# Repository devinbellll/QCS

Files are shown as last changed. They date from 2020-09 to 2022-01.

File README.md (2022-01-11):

# QCS (Quadcopter Control System)
A stabilization and flight control system for a quadcopter, developed in MATLAB and Simulink.

See embedded development and PCB design repo [here](https://github.com/adambujak/FALCON).

Done in collaboration with Adam Bujak ([@adambujak](https://github.com/adambujak) - McMaster University - Mechatronics Engineering).

# Highlights from Development

[Motor Testing and Characterization](https://github.com/devinbellll/QCS/tree/master/Testing/ThrottleSpeedTest)

[Rotor Testing and Characterization](https://github.com/devinbellll/QCS/tree/master/Testing/RotorTest)

## Characterizing the rotor power profile for system modeling

https://user-images.githubusercontent.com/47790946/148705799-1a313020-7e75-4045-ad6e-294311040c41.mp4

## Custom PCB arrived from California courtesy of Adam Bujak

PCB

## First desk-top test on 3D-printed test stand

https://user-images.githubusercontent.com/47790946/148705807-855fa435-2b67-44c3-ac4a-68730c8c19b8.mp4

## Flight Control System stabilizing drone on test stand without assistance

https://user-images.githubusercontent.com/47790946/148705802-f173073f-fe2c-465a-9571-49fa52ba8208.mp4

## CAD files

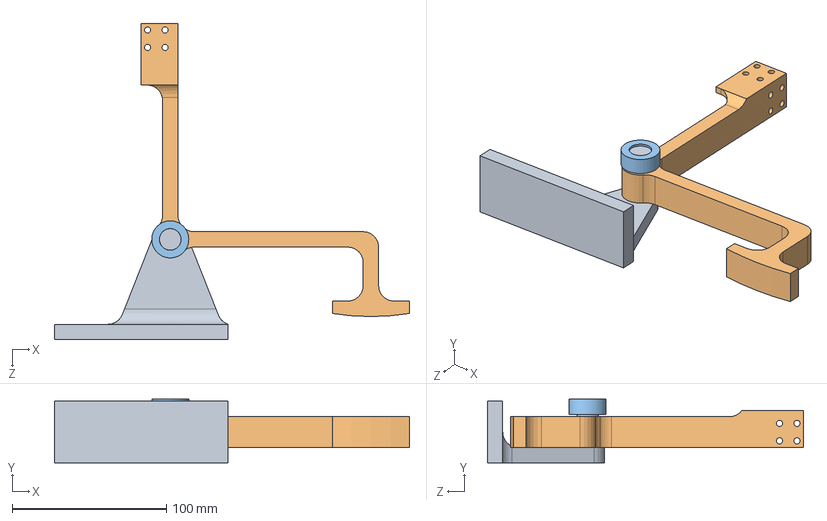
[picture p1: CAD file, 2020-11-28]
Testing/RotorTest/Models/RotorTestRig.SLDASM
230.0 x 41.4 x 205.0 mm
Base
Lever
Cap

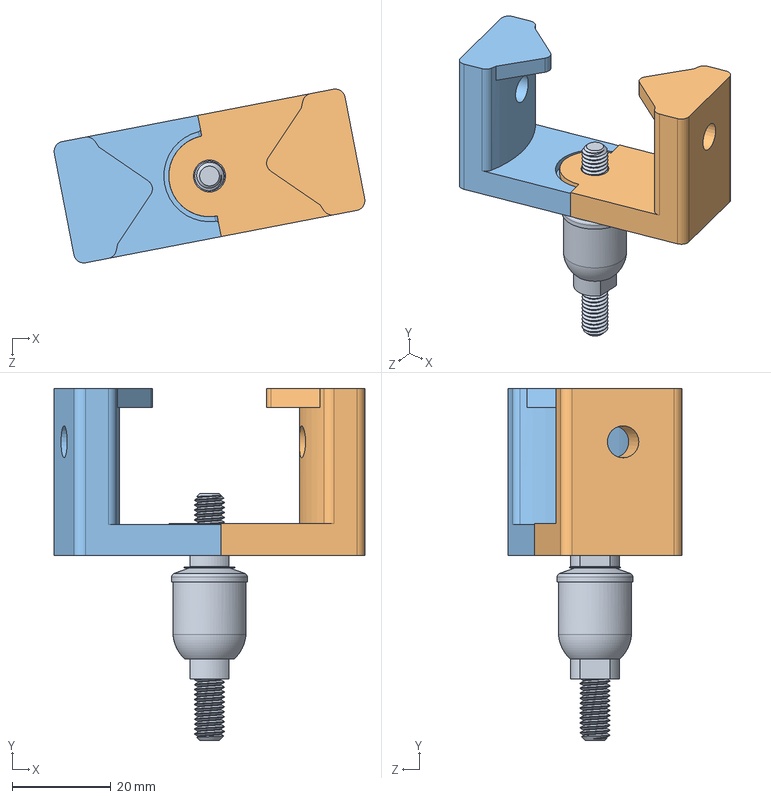
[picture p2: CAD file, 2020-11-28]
Testing/TestStand/TestStand.SLDASM
63.0 x 71.3 x 35.2 mm
BallJoint
DroneMountBracket_d
DroneMountBracket_s

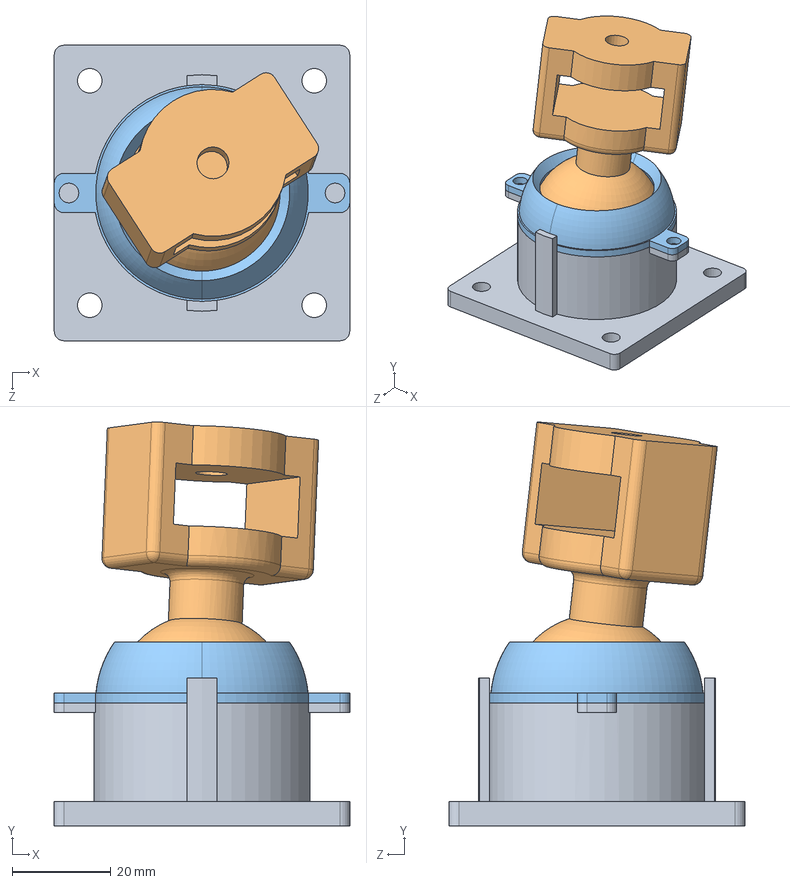
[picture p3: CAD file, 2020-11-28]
Testing/TestStand/TestBallJoint.SLDASM
60.0 x 82.0 x 60.0 mm
Socket
Ball
SocketCap x 2

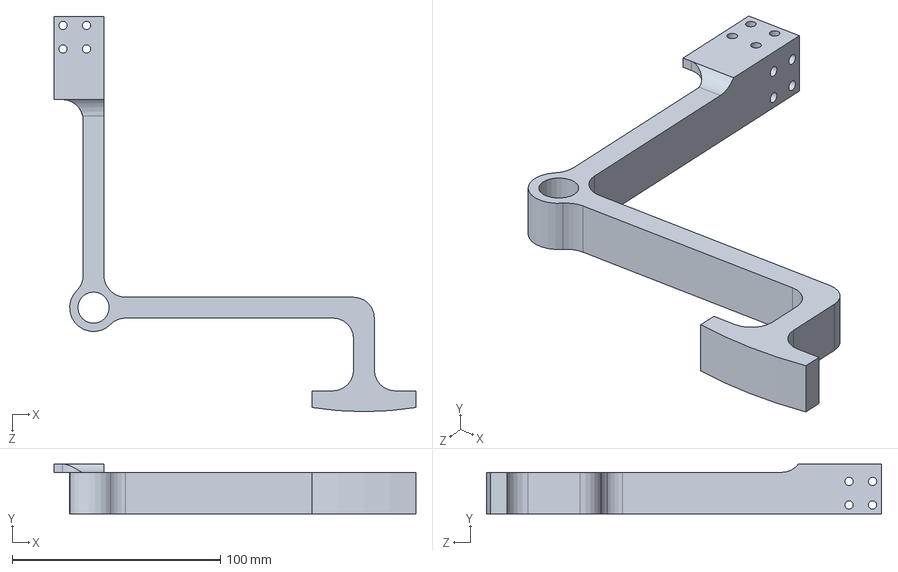
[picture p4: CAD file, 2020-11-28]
Testing/RotorTest/Models/Lever.SLDPRT
174.0 x 24.0 x 190.0 mm

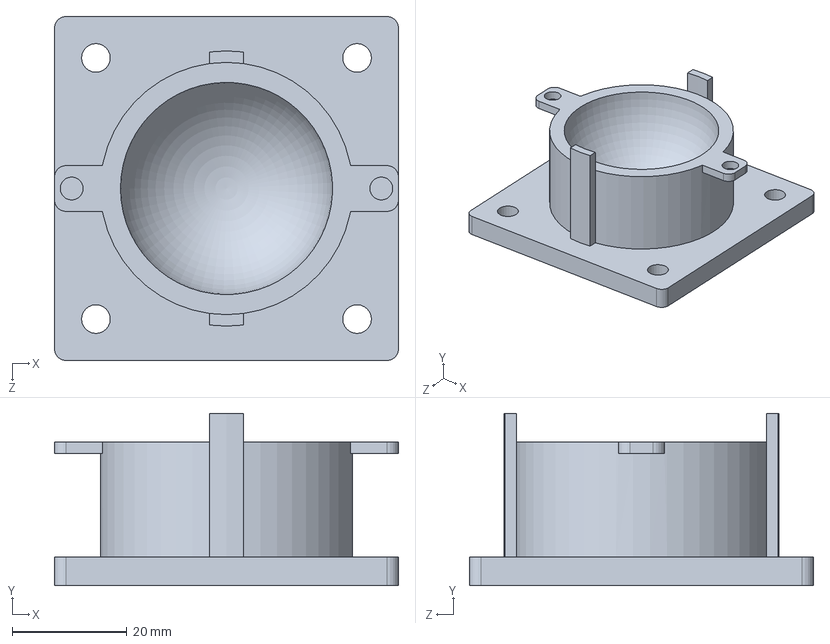
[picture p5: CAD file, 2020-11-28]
Testing/TestStand/Socket.SLDPRT
60.0 x 30.0 x 60.0 mm

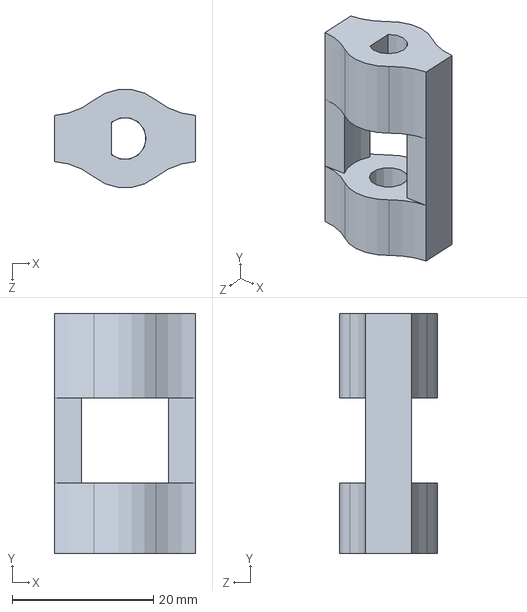
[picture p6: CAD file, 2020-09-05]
Testing/ThrottleSpeedTest/Models/speedTestCoupling.SLDPRT
20.0 x 34.0 x 13.9 mm

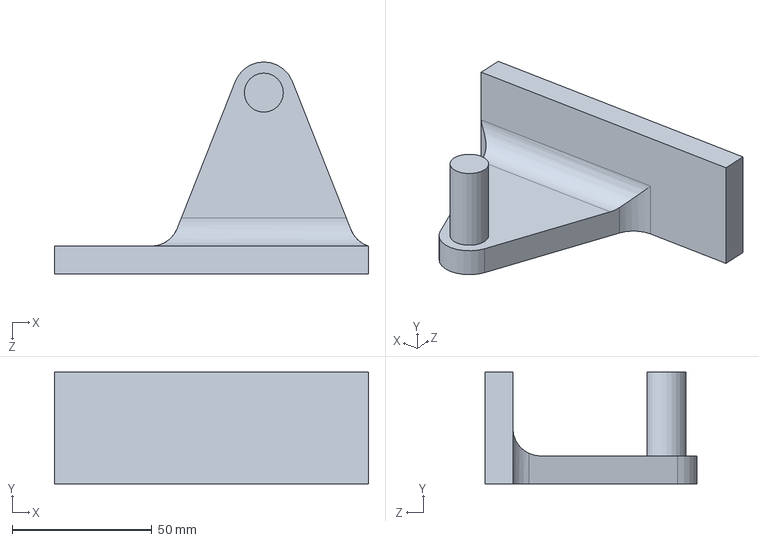
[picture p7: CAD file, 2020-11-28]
Testing/RotorTest/Models/Base.SLDPRT
112.5 x 40.0 x 76.0 mm

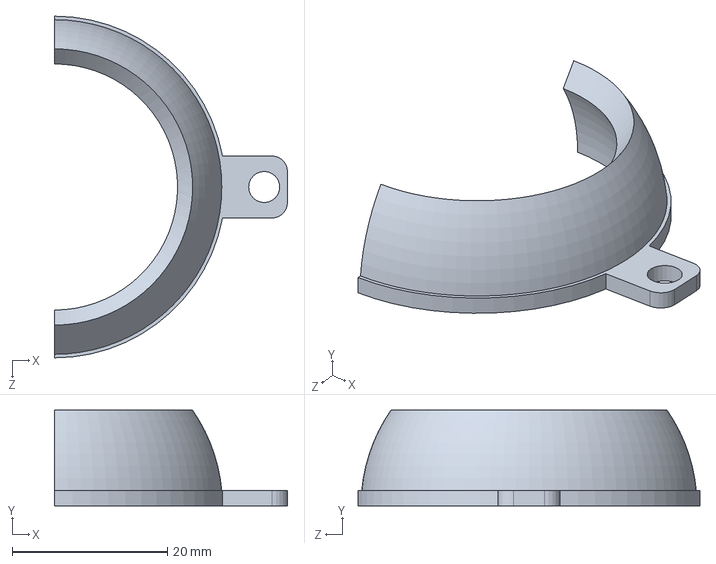
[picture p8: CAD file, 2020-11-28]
Testing/TestStand/SocketCap.SLDPRT
30.0 x 12.3 x 44.0 mm

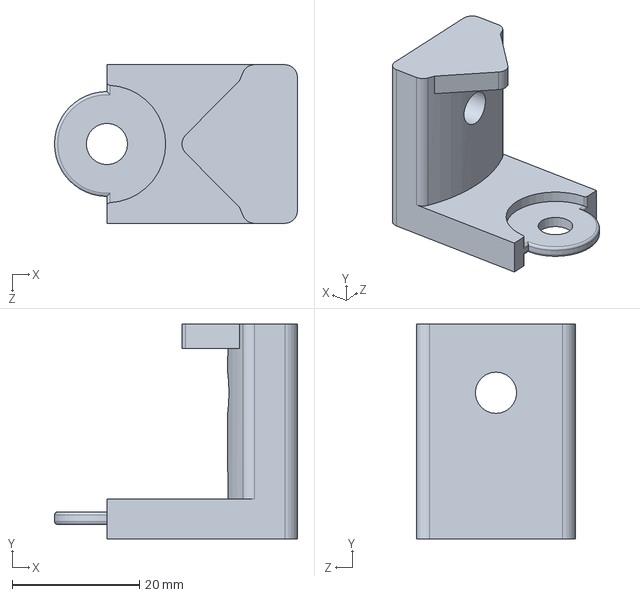
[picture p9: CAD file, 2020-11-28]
Testing/TestStand/DroneMountBracket_s.SLDPRT
38.2 x 33.8 x 25.0 mm

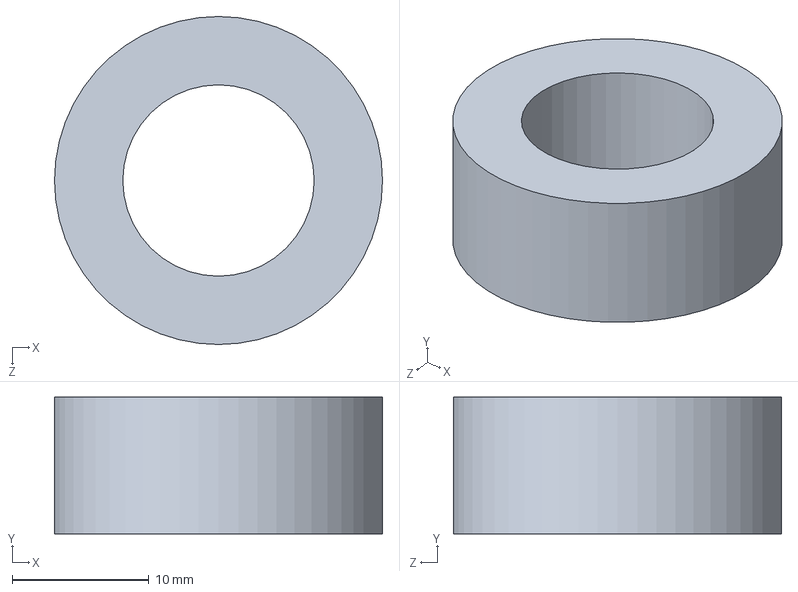
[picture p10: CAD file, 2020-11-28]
Testing/RotorTest/Models/Cap.SLDPRT
24.0 x 10.0 x 24.0 mm

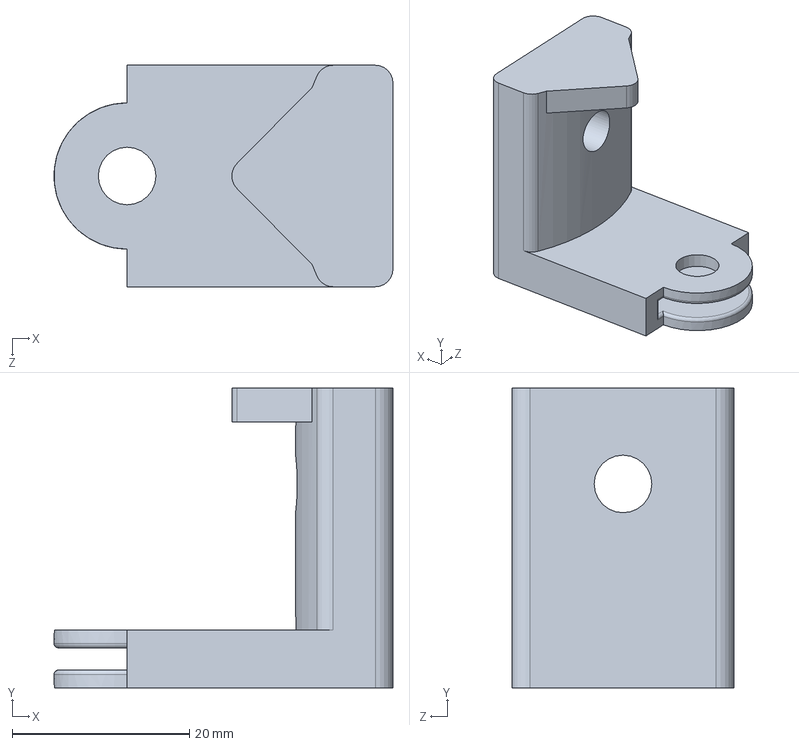
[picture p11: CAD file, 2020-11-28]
Testing/TestStand/DroneMountBracket_d.SLDPRT
38.2 x 33.8 x 25.0 mm

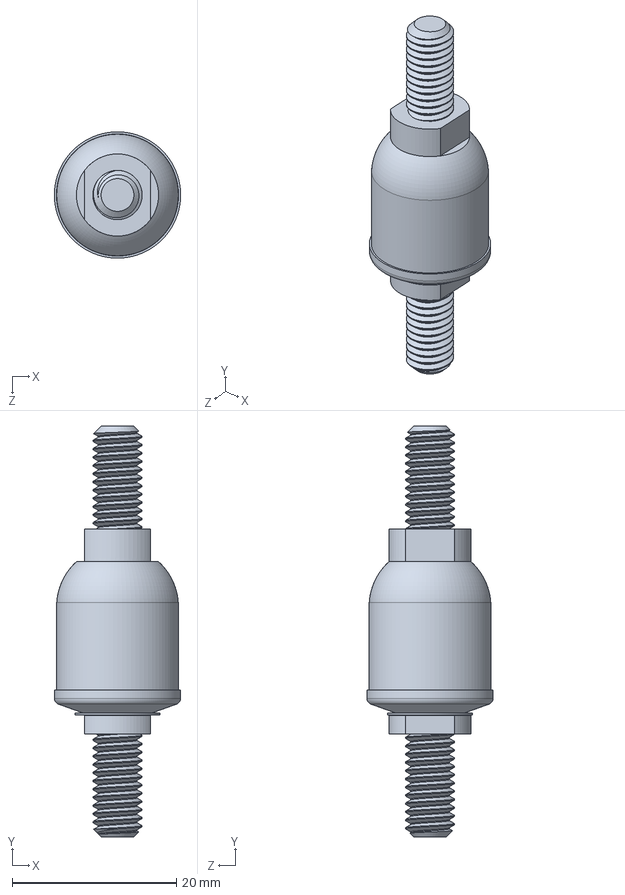
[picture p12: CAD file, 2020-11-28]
Testing/TestStand/BallJoint.SLDPRT
15.4 x 50.0 x 15.4 mm

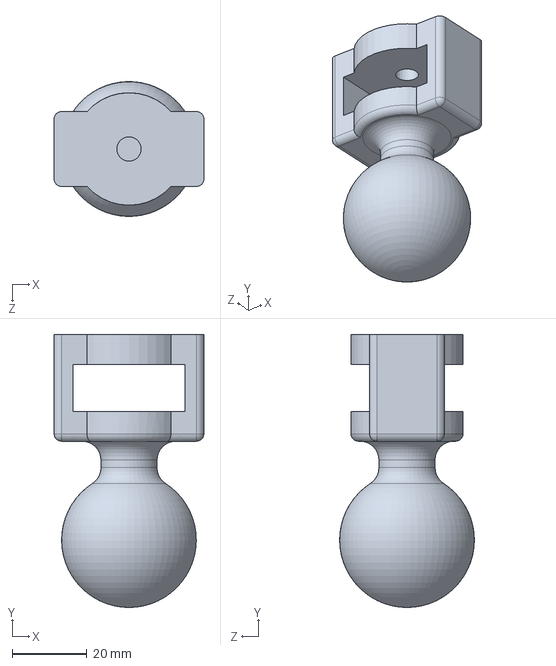
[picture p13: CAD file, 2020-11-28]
Testing/TestStand/Ball.SLDPRT
40.0 x 72.9 x 36.0 mm

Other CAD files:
Testing/RotorTest/Models/Base.STL
Testing/RotorTest/Models/Cap.STL
Testing/RotorTest/Models/Lever.STL
Testing/TestStand/Ball.STL
Testing/TestStand/DroneMountBracket_d.STL
Testing/TestStand/DroneMountBracket_s.STL
Testing/TestStand/Socket.STL
Testing/TestStand/SocketCap.STL
Testing/ThrottleSpeedTest/Models/speedTestCoupling.STL

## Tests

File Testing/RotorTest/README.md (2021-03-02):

# QCS Rotor Testing

### Testing the rotors to determine the relationship between throttle signal, rotor force, and rotor torque.

#### The following are the equations for converting a desired torque or force into a throttle signal (standard SI units):

## Throttle = -4.8568*F^2 + 114.92*F + 90.043

## Throttle = -71209*T^2 + 12848*T + 67.783

#### Relationship between force and torque:

## T = 0.0005*F^2 + 0.0078*F + 0.0025

### The above results were obtained using a test rig to transfer the force and torque of the rotor to a digital scale.
### The rotor was oriented horizontally to avoid ground effects.

#### Setup for measuring force:

F1
F2
F3

#### Setup for measuring torque:

T1
T2

#### The measured data:

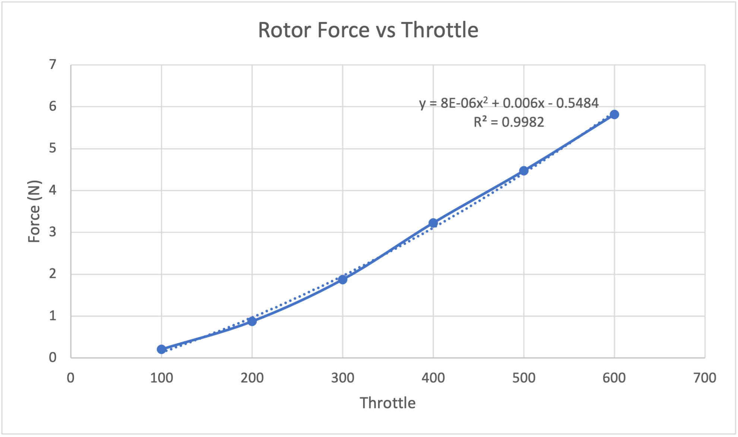
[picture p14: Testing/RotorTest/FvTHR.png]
FvTHR

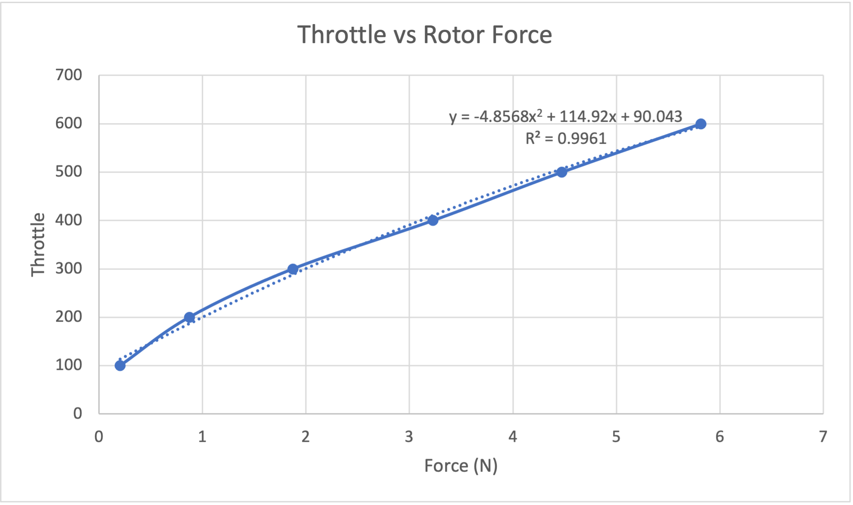
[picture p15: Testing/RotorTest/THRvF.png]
THRvF

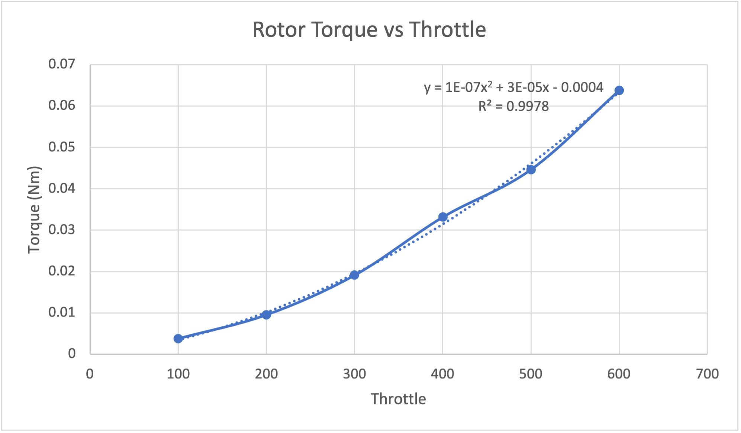
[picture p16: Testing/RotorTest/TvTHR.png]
TvTHR

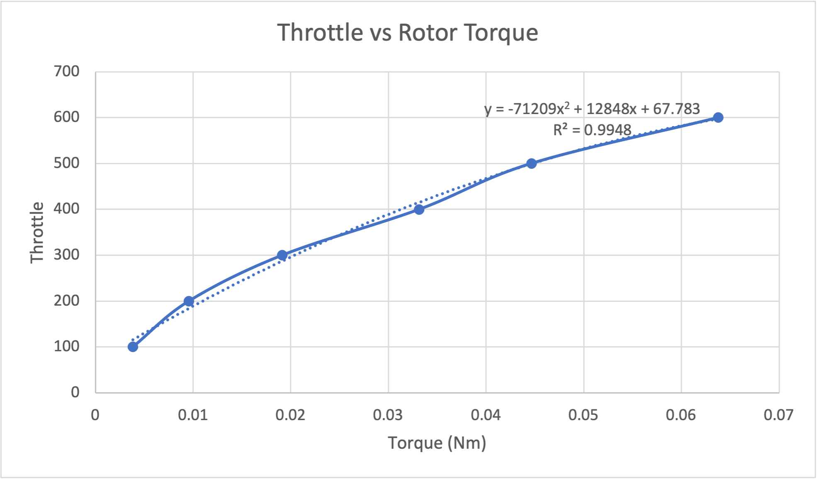
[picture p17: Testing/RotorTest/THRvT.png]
THRvT

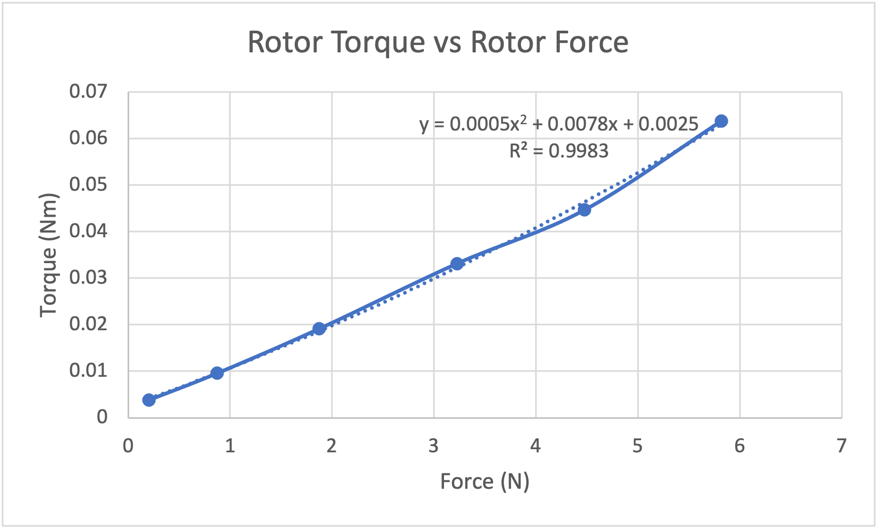
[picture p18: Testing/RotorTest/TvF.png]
TvF


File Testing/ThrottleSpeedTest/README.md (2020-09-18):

# QCS Motor Testing
#### Testing the motors to determine the relationship between input signal and shaft output speed to use for simulation and control system tuning.

#### The ESC accepts a 20ms period PWM signal with pulse widths ranging between 1000-2000us.

#### A test was performed to determine the gain from microseconds input signal to rad/s output speed. The measuring device used was a rotary optical encoder which was attached to the motor shaft with a simple 3D printing coupling. The two devices were mounted together in a simple frame and controlled with an NodeMCU microcontroller running some simple Arduino code.

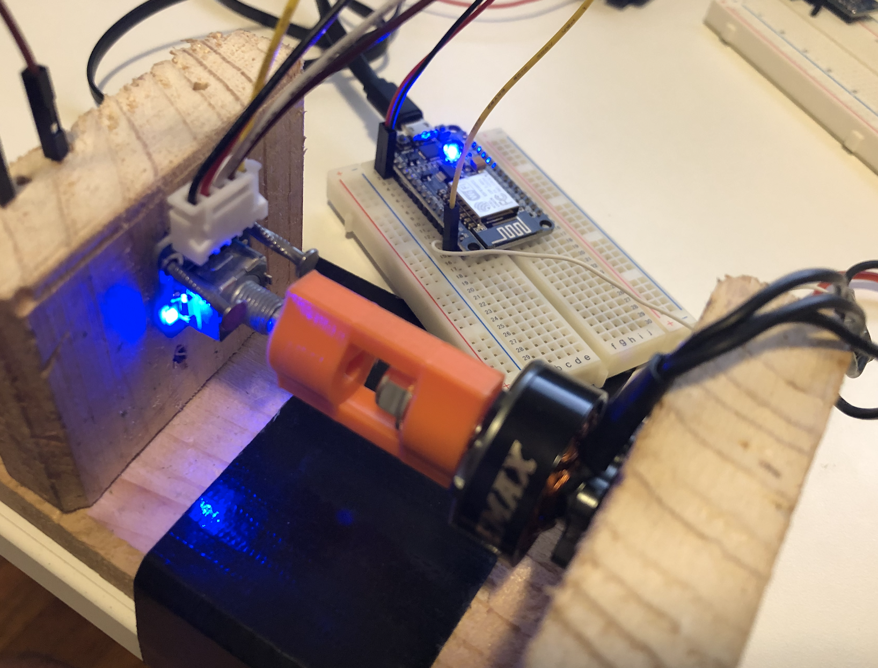
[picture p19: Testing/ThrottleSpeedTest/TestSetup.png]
Test Setup


#### The output of the rotary encoder computed as rad/s within the program and logged to the serial monitor. The test consisted of 10 samples taken at every 10us increment between 1000 and 2000. However, due to limitations in the test rig, readings were only able to be made up to 1400us. Each sample consisted of counting the number of encoder pulses during a 100ms window and converting to rad/s using the below formula.

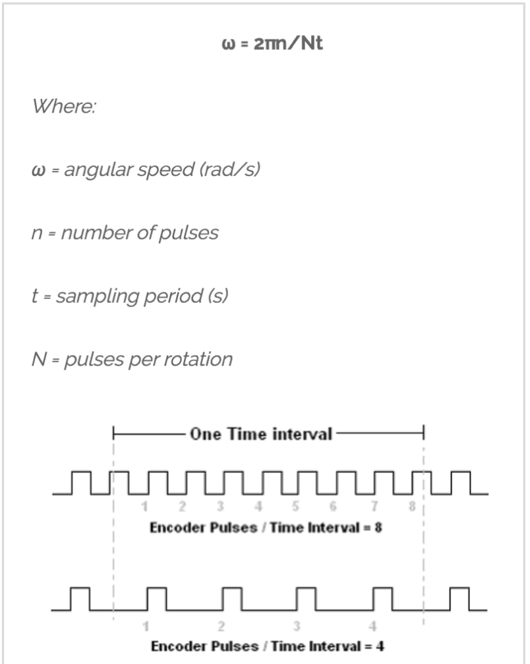
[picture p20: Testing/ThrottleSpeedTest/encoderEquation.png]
Encoder Equation


#### The results are shown in the graph below. The input signal is shown as the number of microseconds that the pulse width is greater than one thousand as 1000us pulse width represents zero throttle. The motor has a deadzone at less than 1030us pulse width where the motor does not spin continuously. 

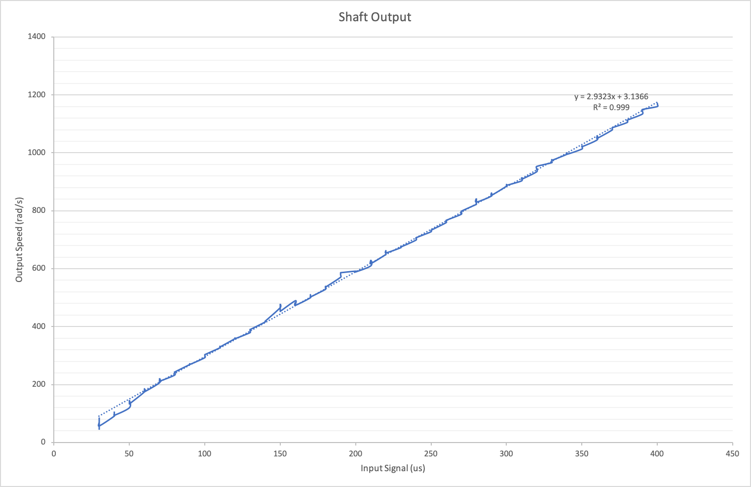
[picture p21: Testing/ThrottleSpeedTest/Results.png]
Results


#### The throttle signals in the control system and airframe model will be represented as an integer between 0 and 1000. The gain to convert from throttle signals to motor shaft speed in rad/s used in the model will be set to 3 and the throttle signals will pass through a saturation block to ensure signals are between 30 and 1000 to avoid the deadzone.

#### The relationship found in this test supports what would be the approximate expected output speed range of a 2400kV running on a 14.8V battery.

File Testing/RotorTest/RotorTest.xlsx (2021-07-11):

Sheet: Test
Throttle | F (g) | F (kg) | F (N) | Ftotal (N)
100 | 21 | 0.021 | 0.20601 | 0.82404
200 | 89 | 0.089 | 0.87309 | 3.49236
300 | 191 | 0.191 | 1.87371 | 7.49484
400 | 329 | 0.329 | 3.22749 | 12.90996
500 | 456 | 0.456 | 4.47336 | 17.89344
600 | 593 | 0.593 | 5.81733 | 23.26932
700 | 745 | 0.745 | 7.30845 | 29.2338
800 | 860 | 0.86 | 8.4366 | 33.7464
Throttle | F (g) | F (kg) | F (N) | T (Nm) | Arm Length (m)
100 | 3 | 0.003 | 0.02943 | 0.0038259 | 0.13
200 | 7.5 | 0.0075 | 0.073575 | 0.00956475
300 | 15 | 0.015 | 0.14715 | 0.0191295
400 | 26 | 0.026 | 0.25506 | 0.0331578
500 | 35 | 0.035 | 0.34335 | 0.0446355
600 | 50 | 0.05 | 0.4905 | 0.063765

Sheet: Mass
 | Mass (g) |  | Total (g)
Battery | 141 |  | 513
Straps | 8
Hedwig | 16
Antenna | 8
Airframe+Electrics+Motors+Props | 340
motors | 36 | 144 | 276
frame | 132

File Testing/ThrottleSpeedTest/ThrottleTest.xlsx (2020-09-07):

Test 1 - Succesful up to 1400us |  |  | Test 2 - Failed, broken encoder
1000 | 0 | 0 | 1000 | 0
1000 | 0 | 0 | 1000 | 0
1000 | 0 | 0 | 1000 | 0
1000 | 0 | 0 | 1000 | 0
1000 | 0 | 0 | 1000 | 0
1010 | 10 | 0 | 1010 | 0
1010 | 10 | 0 | 1010 | 0
1010 | 10 | 0 | 1010 | 0
1010 | 10 | 0 | 1010 | 0
1010 | 10 | 0 | 1010 | 0
1010 | 10 | 0 | 1010 | 0
1020 | 20 | 68.06782667 | 1020 | 0
1020 | 20 | 81.15779333 | 1020 | 0
1020 | 20 | 31.41592 | 1020 | 0
1020 | 20 | 128.2816733 | 1020 | 0
1020 | 20 | 62.83184 | 1020 | 2.617993333
1020 | 20 | 178.0235467 | 1020 | 47.12388
1030 | 30 | 60.21384667 | 1030 | 60.21384667
1030 | 30 | 44.50588667 | 1030 | 0
1030 | 30 | 49.74187333 | 1030 | 23.56194
1030 | 30 | 86.39378 | 1030 | 41.88789333
1030 | 30 | 70.68582 | 1030 | 94.24776
1030 | 30 | 57.59585333 | 1030 | 62.83184
1040 | 40 | 91.62976667 | 1040 | 91.62976667
1040 | 40 | 96.86575333 | 1040 | 68.06782667
1040 | 40 | 96.86575333 | 1040 | 60.21384667
1040 | 40 | 107.3377267 | 1040 | 52.35986667
1040 | 40 | 99.48374667 | 1040 | 65.44983333
1040 | 40 | 94.24776 | 1040 | 54.97786
1050 | 50 | 120.4276933 | 1050 | 70.68582
1050 | 50 | 146.6076267 | 1050 | 78.5398
1050 | 50 | 141.37164 | 1050 | 125.66368
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

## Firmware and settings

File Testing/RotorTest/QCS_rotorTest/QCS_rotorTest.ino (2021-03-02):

#include <Servo.h>

int throttleZero = 1000;
int throttleMax = 2000;
int throttleIn;

Servo ESC;
int ESC_Pin = 2;

void setup()
{
  pinMode(ESC_Pin, OUTPUT);
  Serial.begin(115200);
  ESC.attach(ESC_Pin);
  delay(100);
  ESC.writeMicroseconds(throttleZero);
  Serial.println("Throttle low, ready for test");
  
// SECTION FOR CALIBRATION ESC //
  
//  ESC.writeMicroseconds(throttleMax);
//  while(!Serial.available()) {
//    Serial.println("Calibrating, throttle high... Enter 'l' when ready");
//    delay(500);
//  }
//  if(Serial.read() == 'l') {
//      ESC.writeMicroseconds(throttleZero);
//      Serial.println("Throttle low, ready for test");
//  }

//////////////////////////////////

}

void loop()
{
  
  if(Serial.available()) {

    throttleIn = Serial.parseInt();
  
    if(throttleIn == -1) {
      Serial.println("Done, Exiting");
      ESC.writeMicroseconds(throttleZero);
      while(1) {
        yield();
      }
    }
    
    else {
      
      Serial.print("Throttle set to: "); Serial.println(throttleIn);
      Serial.println();
      ESC.writeMicroseconds(throttleZero + throttleIn);
      
    }
  }
}

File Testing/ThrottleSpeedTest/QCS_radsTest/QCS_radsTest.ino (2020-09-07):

#include <Servo.h>

int currTime;
int prevTime;
int currLevel;
int prevLevel;
int pulseCount;
int throttleSignal = 1000;
int measureCount;
Servo ESC;

int samplePeriod = 100;

void setup()
{
  pinMode(D0, INPUT);
  pinMode(D2, OUTPUT);
  Serial.begin(115200);
  ESC.attach(D2);
  ESC.writeMicroseconds(throttleSignal);
  delay(5000);
}

void loop()
{
  while (throttleSignal <= 1400)
  {
    ESC.writeMicroseconds(throttleSignal);
    measureCount = 0;
    while (measureCount <= 5)
    {
      prevTime = millis();
      pulseCount = 0;
      while ((currTime - prevTime) < samplePeriod)
      {
        currLevel = digitalRead(D0);
        if (currLevel == LOW && prevLevel == HIGH)
        {
          prevLevel = LOW;
        }
        else if (currLevel == HIGH && prevLevel == LOW) 
        {
          prevLevel = HIGH;
          pulseCount++;
        }
        currTime = millis();
      }
      
      Serial.print(throttleSignal);
      Serial.print("\t");
      Serial.println(pulse2rads(pulseCount, samplePeriod), DEC);
      measureCount++;
    }
    throttleSignal += 10;
    yield();
  }
  throttleSignal = 1000;
  ESC.writeMicroseconds(throttleSignal);
  while(1)
  {
    yield();
  }
}

double pulse2rads(int n, int Ts)
{
  double w;
  double t;
  int N = 24; //number of pusles per rotation of encoder
  t = (double)(Ts/1000.d); //convert period to seconds

  w = (2*3.141592*n)/(N*t);

  return w;
}

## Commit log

2020-09-05 added motor2encoder coupling model for speed test
    [speedTestCoupling.SLDPRT]
2020-09-05 saved speedTestCoupling as STL file for printing
    [speedTestCoupling.STL]
2020-09-07 moved around files and added test info from motor speed test
    [ThrottleTest.xlsx, speedTestCoupling.SLDPRT, speedTestCoupling.STL]
2020-09-19 added Sensor library to model
2020-09-19 changes to motor cmd - w block and fixed sensor bus definition
2020-09-21 removed altimeter function block, fixed signals going into IMU block
2020-10-27 removed buses functions for buses.mat, added estimator vars file, added sensor and rotor stuff
2020-10-28 sensors feedthrough to get flight control working, pitch and roll control now working
2020-11-27 current config generating reasonable code
2020-11-28 grabbed ball joint
    [Ball.SLDPRT, Ball.STL, BallJoint.SLDPRT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]
2020-11-28 added rotor power test rig
    [Base.SLDPRT, Base.STL, Cap.SLDPRT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]
2020-11-28 modified to fit on printer
    [Base.SLDPRT, Base.STL, Lever.SLDPRT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]
2021-01-09 moved sensor lib to own folder
2021-03-02 added rotor test results
    [Base.SLDPRT, Base.STL, Cap.SLDPRT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]
2021-03-02 added fidelity to sensors and reorganized startup scripts
2021-03-03 added new mass properties based on real frame, updated control system with rotor equations, made controller task file
2021-03-04 corrected sensor noise setup
2021-03-06 added more precision to rotor measurements
    [RotorTest.xlsx]
2021-03-06 created simpler actuator model
    [motorLib.slx.type.File.xml]
2021-03-06 got model set up for motion ref with new motor/rotor models
2021-03-07 updated env and sensors for variant subsytem setups
2021-03-07 alt PID tuned somehow
2021-03-08 added old motor system back in as varient
2021-03-09 updated sensors to give IMU its own Ts
2021-03-10 measured sensor input from hardware and got sensor models behaving very similarly
2021-03-10 added filters to sensor preprocessing, made altitude estimator a custom complimentary filter
2021-03-13 switched to 100Hz
2021-03-13 added another complimentary filter to altitude to correct velocity drift
2021-04-28 added tunable parameters for control
    [RotorTest.xlsx]
2022-01-11 added PCB pictures
